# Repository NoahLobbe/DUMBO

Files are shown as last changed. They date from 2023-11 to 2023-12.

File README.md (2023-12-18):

# DUMBO
**D**efinitely **U**seless **M**ouse ro**B**ot **O**kay.

Project built off an RC car. Unsure of this specifics as I bought it a second hand shop (bargain!) eons ago (in a galaxy far, far away...).
These are my two guesses, but I think the FCC had other RC cars with similiar chassis, so really hard to find the exact one.
- Scientific Toys (n.d.), *R/C 2.4GHz 1:12 Sand Blaster*, http://www.scientific.com.hk/en/products/97213, accessed 24 May 2023
- FCC (2017), *FCC ID BY35058-24GR R/C Vehicle by Scientific Toys Ltd.*, FCC ID, https://fccid.io/BY35058-24GR, accessed 24 May 2023

## Design Process
Contains concept sketches, mechanical drawings (hand drawn), schematics, and flowchart. Some basic pieces of the design process.

## Protoype
All inside the folder `Prototype`. 
- Contains an .STL to 3D print to hold the rear assembly, of the RC car, in place, replacing the need of the original chassis cover.
- Code is a bit of a mess, so attempt to understand at your own peril.

## Finals
BEWARNED, things are messy; view at your own peril :D

### 3D Printing
Contains .STL's and some slicing images

### Code
`powerHD-1501MG` is the testing code to calibrate/check the servo is steering correctly.
`Version3_reversing attempt` and `Version4` were coded to use two shift registers in, cascaded. However, they were not needed in the final DUMBO. `shift_registers` is a testing file to make sure they are working, and make it easier to debug, compared to integrating it straight into the main code and figuring out "what the HECK is wrong?!??!?".
`Version6` is the last version. During testing, two Ultrasonics were needed to be registered stuck for DUMBO to be stuck, but performance might be better with only one required. Dunno.

### Images
Here are some:
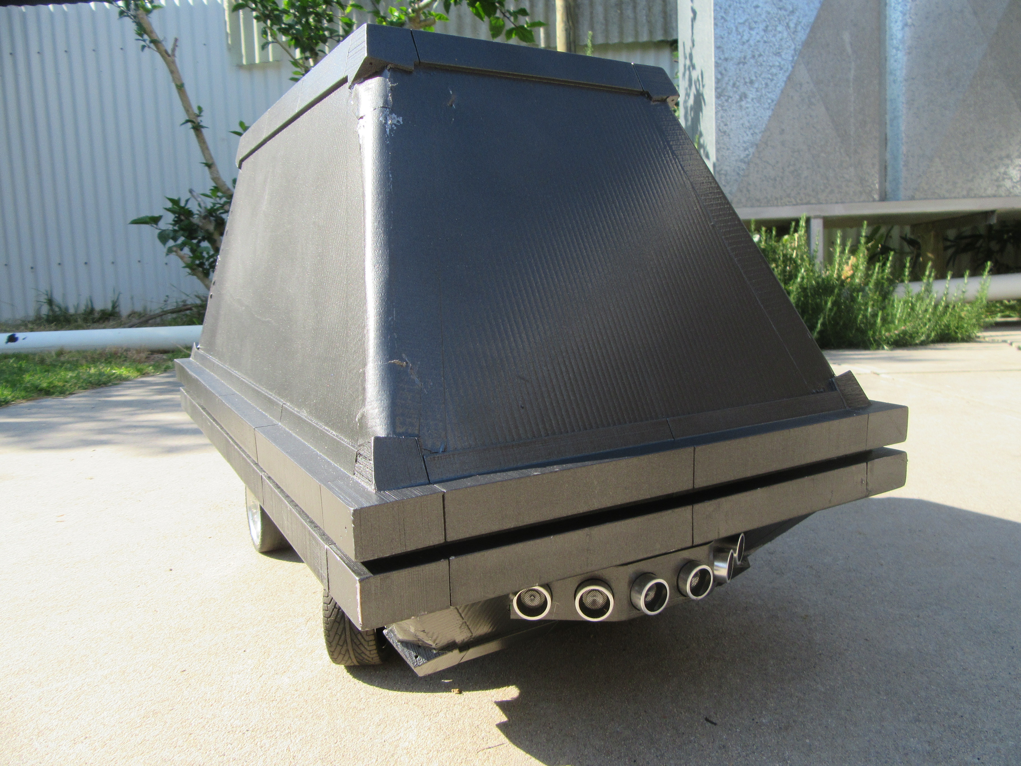
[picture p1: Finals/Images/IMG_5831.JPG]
DUMBO angled image

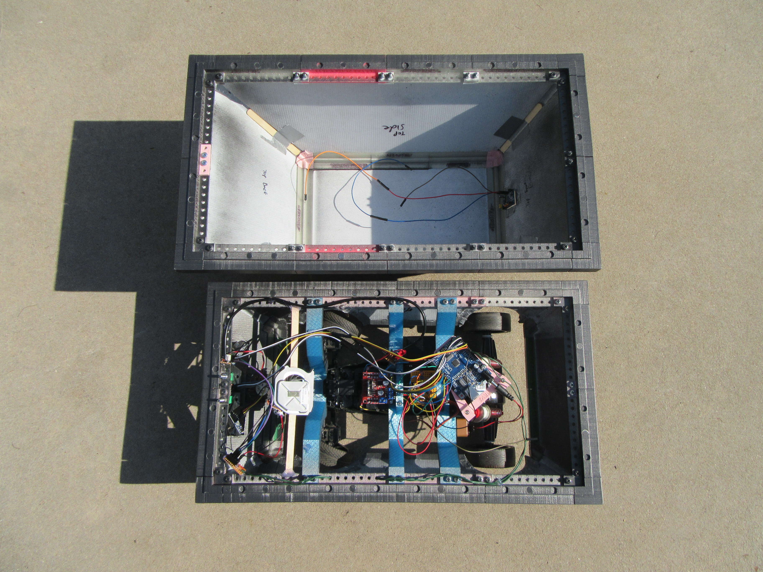
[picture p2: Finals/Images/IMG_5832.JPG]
DUMBO insides

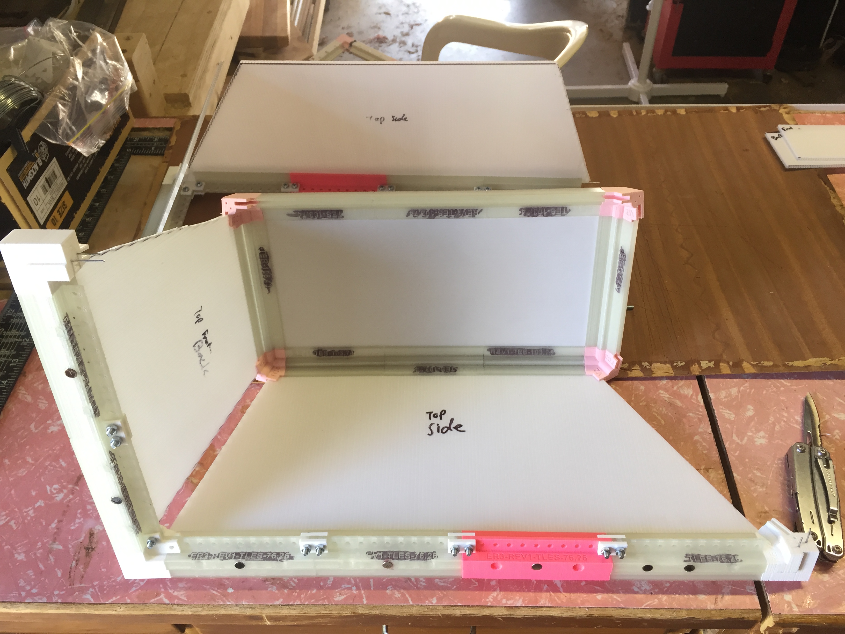
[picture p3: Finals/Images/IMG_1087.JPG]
Top Shell under construction


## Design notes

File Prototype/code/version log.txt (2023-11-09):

Last updated 24 August 2023, Noah Lobbe

How version system works, V.W.XY.Z
 * V is either 'b' or 'm' to indicate a branch or master
 * W is iteration of completed product.
 * X is incremented when a big function/feature/sensor is added
 * Y is just code improvements, no new stuff as that would classify as X
 * Z is the name of the branch, or if master than just = 0

Version log
master
	| m.0.10.0 Added motor driver
	|
	| m.0.11.0 Moved motor driver code into a neat class
	|
	| m.0.20.0 Added PIR motion sensor
	|
	| m.0.21.0 Moved PIR motion sensor code into a neat class
	|	
	| m.0.30.0 Added Ultrasonic sensor
	|
	| m.0.31.0 Code modifications
	| 
	| m.0.32.0 More code modifications. Note for previous versions: if (distance <=minimum_turning_distance_mm) is in wrong spot to ever be executed...

branch_rebuild ##############make sure to mention this annoying bug in final solution
	| b.0.30.rebuild Stripping back to basics. PIR not implemented in main loop.
	|
	| b.0.40.rebuild Reintroducing previous_distance stuff

//really need to add an encoder to the motor output to determine travel distances//

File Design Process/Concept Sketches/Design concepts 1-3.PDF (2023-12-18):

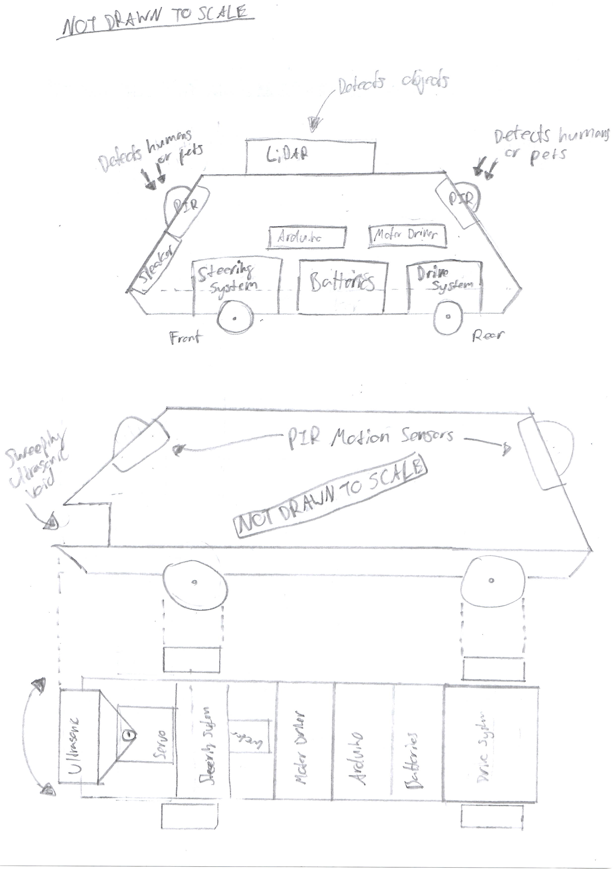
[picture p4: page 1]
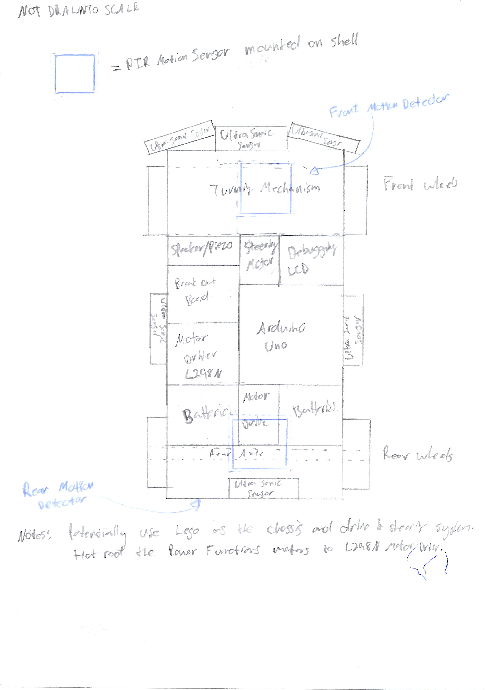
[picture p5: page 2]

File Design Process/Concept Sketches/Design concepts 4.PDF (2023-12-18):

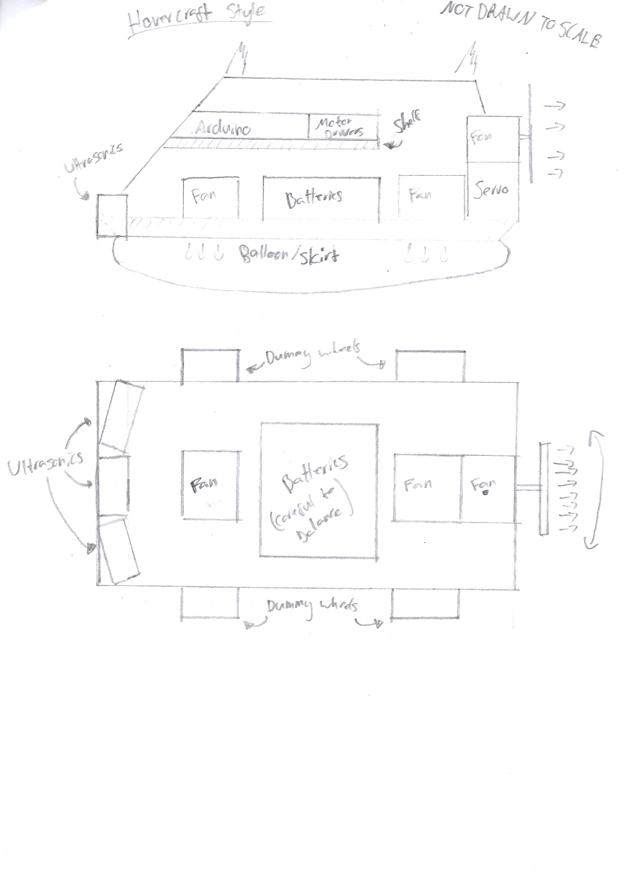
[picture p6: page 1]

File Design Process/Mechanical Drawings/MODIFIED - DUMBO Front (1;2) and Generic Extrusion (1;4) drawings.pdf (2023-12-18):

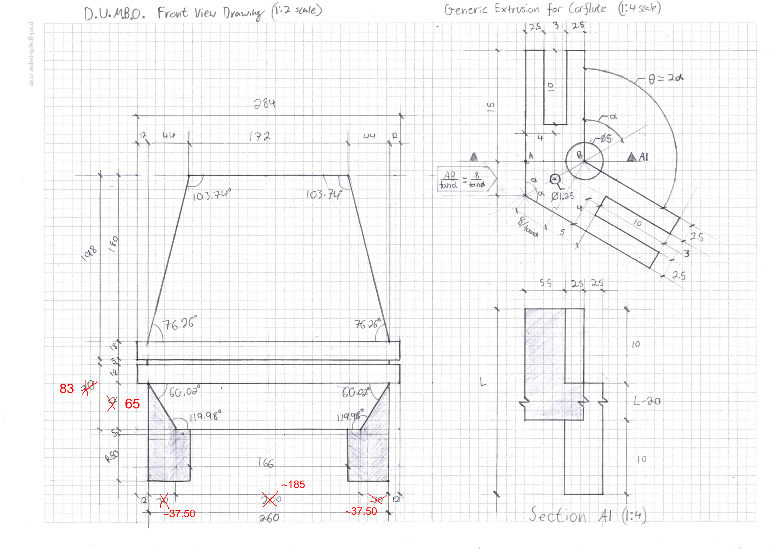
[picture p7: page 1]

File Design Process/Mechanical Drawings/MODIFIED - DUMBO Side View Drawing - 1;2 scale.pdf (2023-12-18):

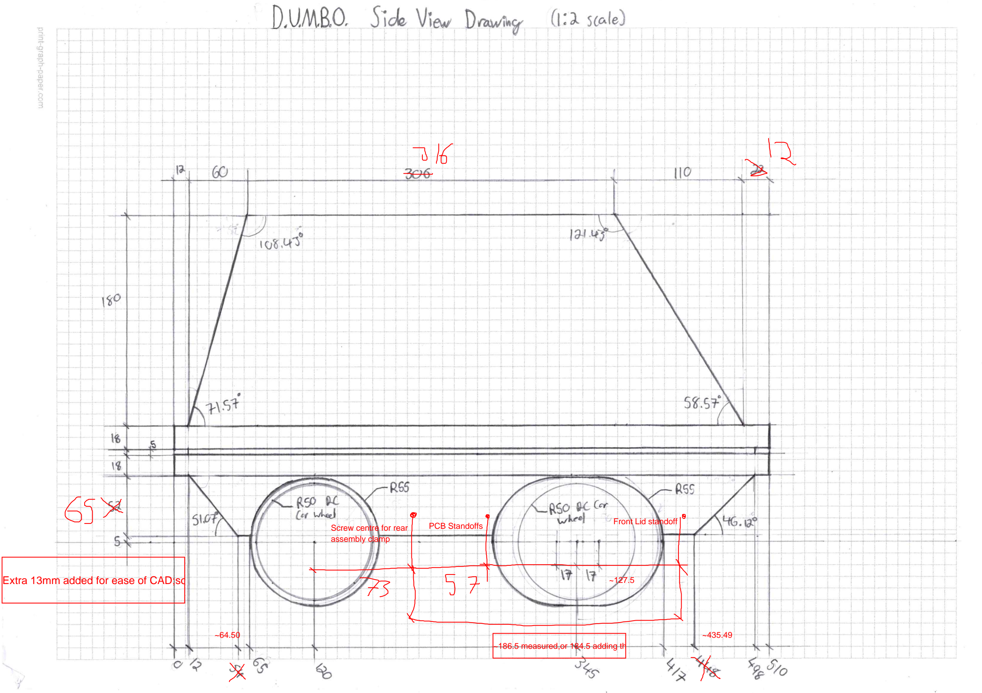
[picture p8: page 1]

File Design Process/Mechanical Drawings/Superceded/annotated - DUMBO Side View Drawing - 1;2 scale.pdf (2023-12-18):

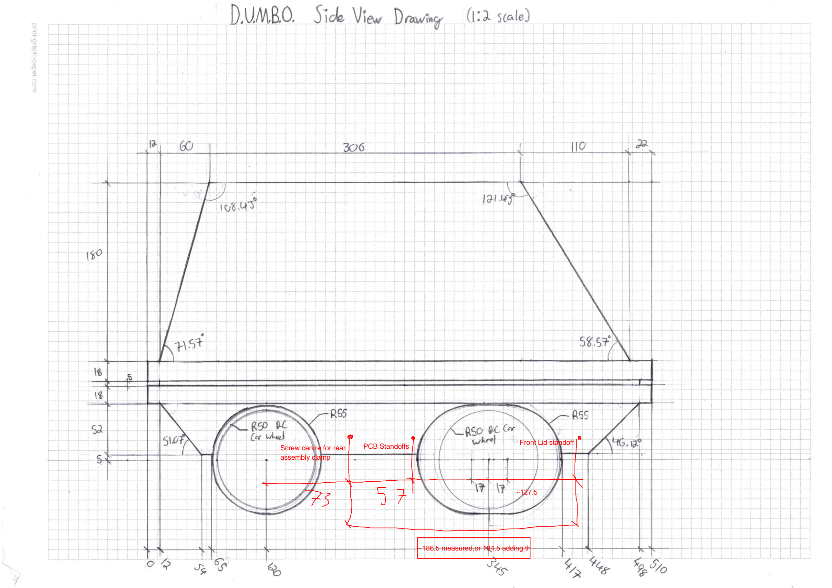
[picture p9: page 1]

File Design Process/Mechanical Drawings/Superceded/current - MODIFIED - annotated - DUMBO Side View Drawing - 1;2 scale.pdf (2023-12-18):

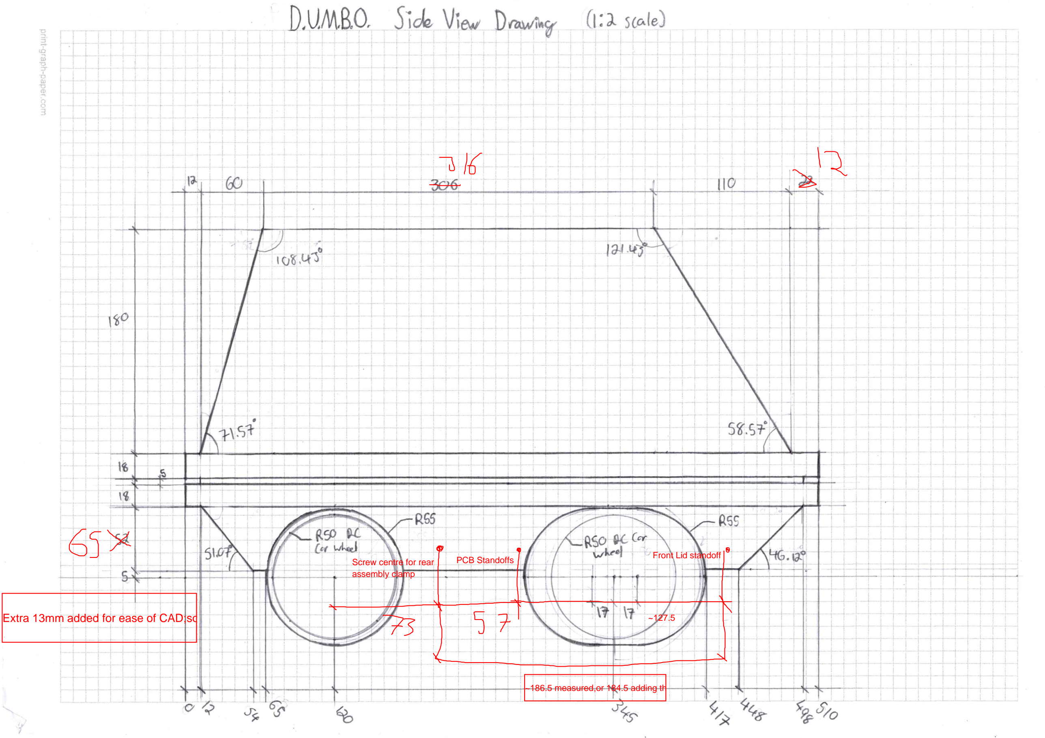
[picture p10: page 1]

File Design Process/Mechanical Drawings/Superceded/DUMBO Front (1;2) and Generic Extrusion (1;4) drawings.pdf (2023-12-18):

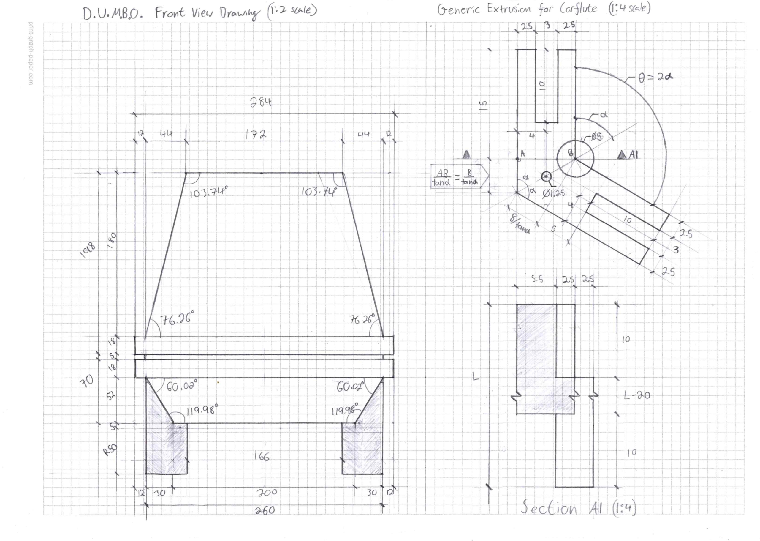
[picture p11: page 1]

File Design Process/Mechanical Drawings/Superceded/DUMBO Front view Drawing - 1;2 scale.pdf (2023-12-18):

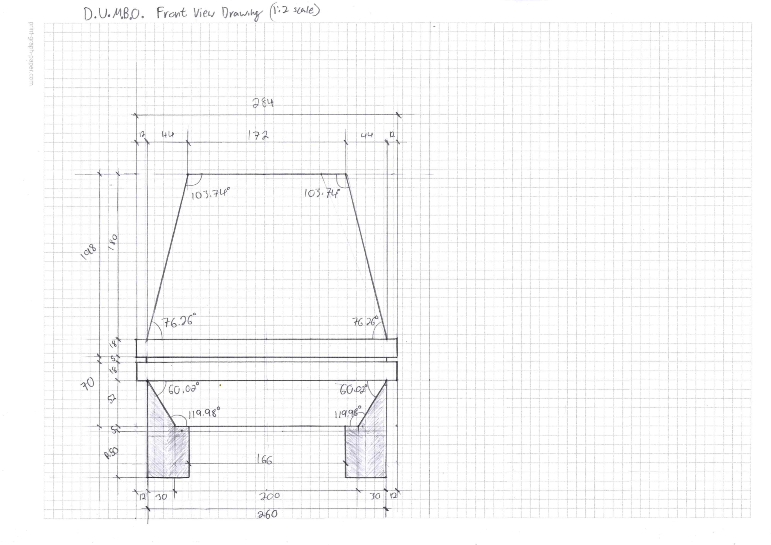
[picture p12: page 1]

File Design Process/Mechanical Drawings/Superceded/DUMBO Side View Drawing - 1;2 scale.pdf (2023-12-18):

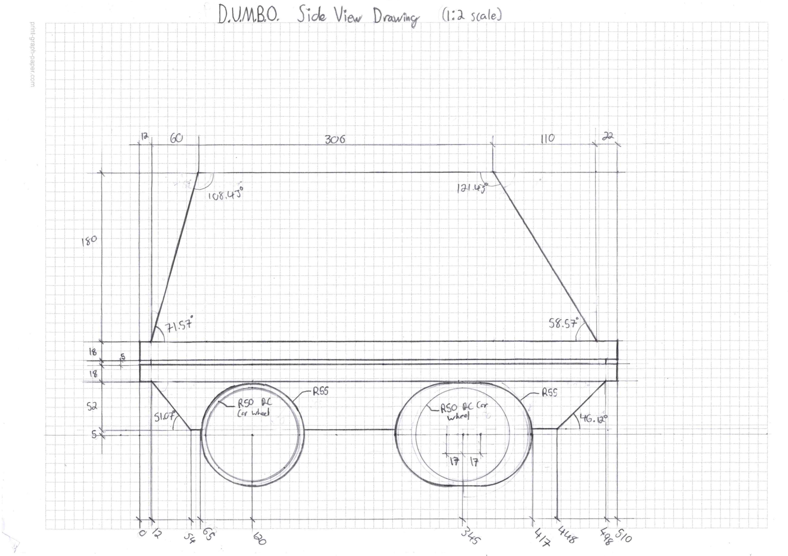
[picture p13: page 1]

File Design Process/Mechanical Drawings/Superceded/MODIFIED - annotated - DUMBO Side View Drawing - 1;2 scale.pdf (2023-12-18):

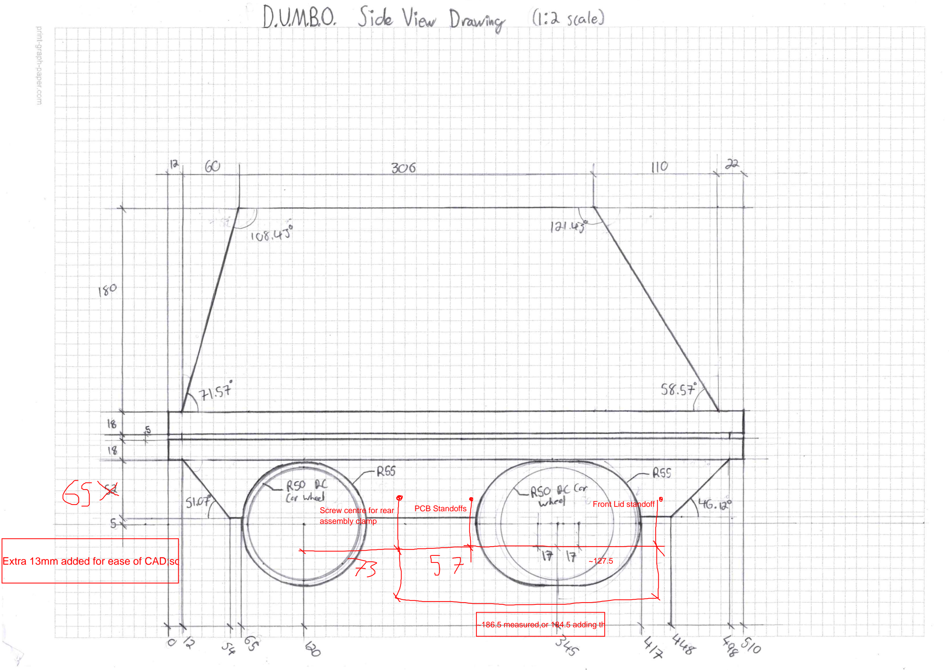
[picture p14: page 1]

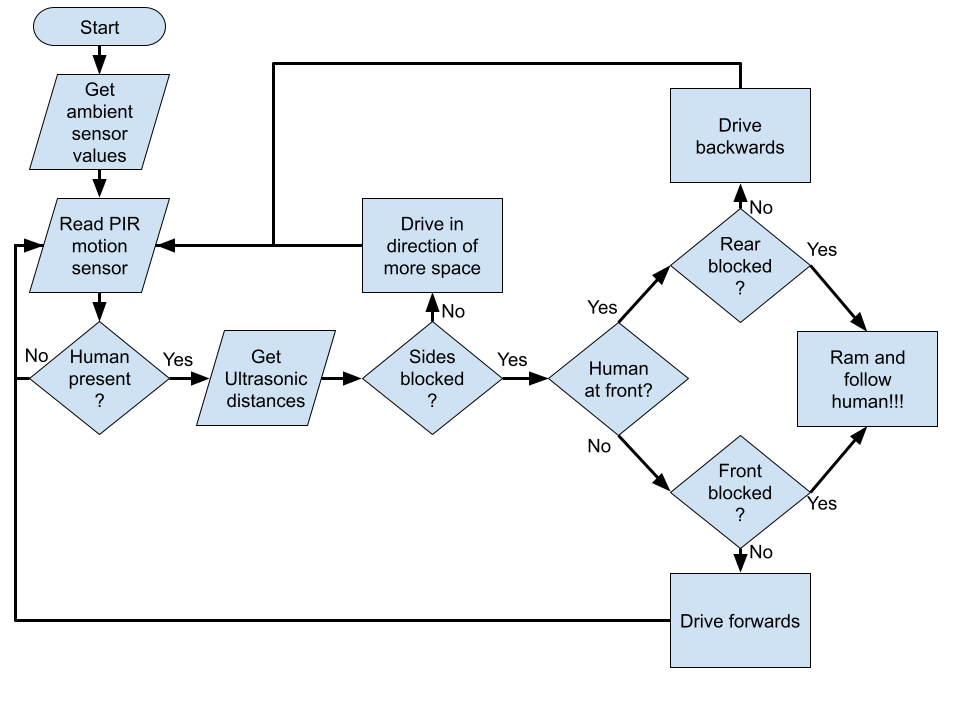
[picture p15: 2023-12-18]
Design Process/Flowchart/Program Flowchart - Major Product 2023.png

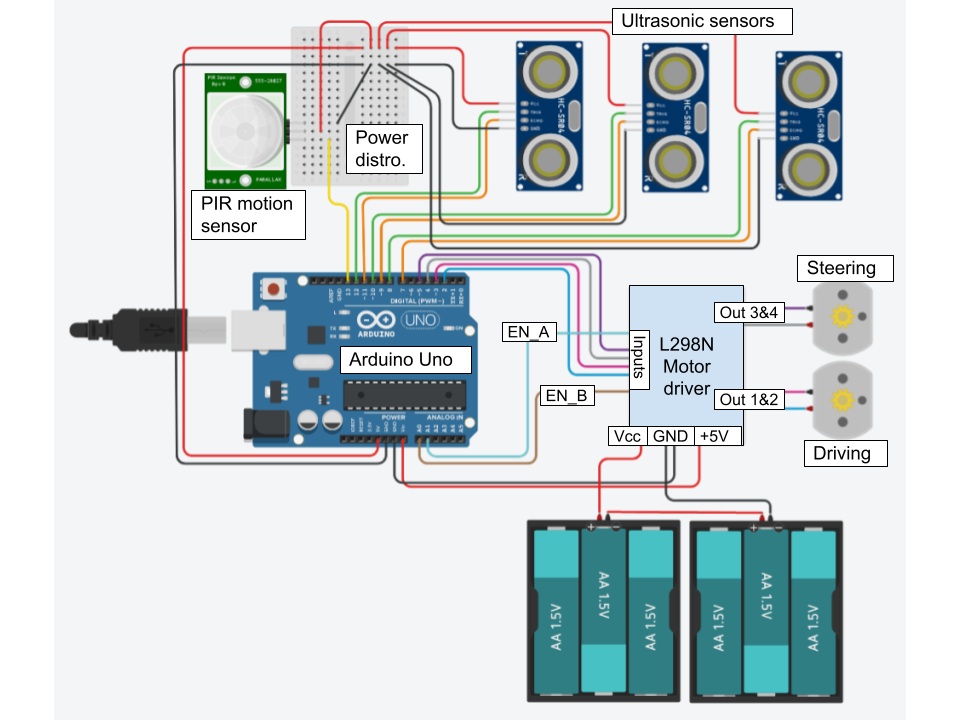
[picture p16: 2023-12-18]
Design Process/Schematic or fritzing/Fritzing for Useless Mouse Droid.png

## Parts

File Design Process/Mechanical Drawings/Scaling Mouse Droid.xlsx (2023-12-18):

Mouse Droid Dimensions |  |  |  |  | RC Car
 |  |  |  |  | width | 260
 |  |  |  |  | length | 325
Dimension | Value (mm) | Scale | Scaled Value (mm) |  | wheelbase | 225
Bottom Shell
Overall Length | 561.20 | 0.90 | 506.99
Pre-overhang length | 535.40 | 0.90 | 483.68
bottom length | 451.14 | 0.90 | 407.56
 |  | 0.90 | 0.00
Overall Width | 313.60 | 0.90 | 283.31
Pre-overhang width | 287.80 | 0.90 | 260.00
bottom Width | 219.80 | 0.90 | 198.57
 |  | 0.90 | 0.00
Overall height | 77.40 | 0.90 | 69.92
bottom-overhang height | 57.20 | 0.90 | 51.67
 |  | 0.90 | 0.00
Overhang depth | 12.90 | 0.90 | 11.65
Overhang height | 20.20 | 0.90 | 18.25
 |  | 0.90 | 0.00
Rear slope angle (from horizontal, measured from bottom) | 56.51 | 0.90 | 51.05
Front slope angle (from horizontal, measured from bottom) | 50.94 | 0.90 | 46.02 |  | Value | Scaled |  | Value | Scaled
 |  | 0.90 | 0.00 | Degrees | 0.9862855603 | 0 | Radians | 37.84549887 | 0 | Horizontal component
 |  | 0.90 | 0.00 | Degrees | 0.889070721 | 0 | Radians | 46.41890985 | 0 | Horizontal component
 |  | 0.90 | 0.00
 |  | 0.90 | 0.00
Arch centre-centre | 306.70 | 0.90 | 277.07
Rear arch radius | 57.20 | 0.90 | 51.67
Front arch radius | 32.60 | 0.90 | 29.45 |  |  |  |  |  | Value | Dimension
Distance from arch centres to bottom | 11.56 | 0.90 | 10.45 |  |  |  |  |  | 86.50 | L
 |  | 0.90 | 0.00 |  |  |  |  |  | 57.20 | r_1
Wheel arch spacing | 220.20 | 0.90 | 198.93 |  |  |  |  |  | 32.60 | r_2
Edge of bottom to rear arch | 12.90 | 0.90 | 11.65 |  |  |  |  |  | 0.2035 | a (angle in radians)
Edge of bottom to front arch | 45.04 | 0.90 | 40.69 |  |  |  |  |  | 0.3626 | c (angle in radians)
 |  | 0.90 | 0.00 |  |  |  |  |  | 11.56 | r_1 sina
Length of rear arch chord | 112.04 | 0.90 | 101.22 |  |  |  |  |  | 11.56 | r_2sinc
Length of front arch chord | 60.96 | 0.90 | 55.07 |  |  |  |  |  | 56.02 | r_1cosa
 |  | 0.90 | 0.00 |  |  |  |  |  | 30.48 | r_2cosc
height from rear arch top to overhang | 11.56 | 0.90 | 10.45
height from front arch top to overhang | 36.16 | 0.90 | 32.67
 |  | 0.90 | 0.00
Top Shell |  | 0.90 | 0.00
Overall Length | 559.5 | 0.90 | 505.46
top length | 324.2 | 0.90 | 292.88
back slope horizontal length | 66.8 | 0.90 | 60.35
front slope horizontal length | 118.3 | 0.90 | 106.87
 |  | 0.90 | 0.00
Overall width | 311.6 | 0.90 | 281.50 |  |  |  |  |  | Value | Dimension
top width | 161.8 | 0.90 | 146.17 |  |  |  |  |  | 1.308996939 | angle of sides from horizontal folded down (in radians)
one side slope width | 48.50 | 0.90 | 43.81
 |  | 0.90 | 0.00
post lip width | 258.80 | 0.90 | 233.80
 |  | 0.90 | 0.00
overall height | 200.7 | 0.90 | 181.31
height exlcluding lip | 181 | 0.90 | 163.52
 |  | 0.90 | 0.00
lip height | 19.7 | 0.90 | 17.80
lip depth (sides) | 26.40 | 0.90 | 23.85
lip depth (back) | 24.9 | 0.90 | 22.49
lip depth (front) | 25.3 | 0.90 | 22.86

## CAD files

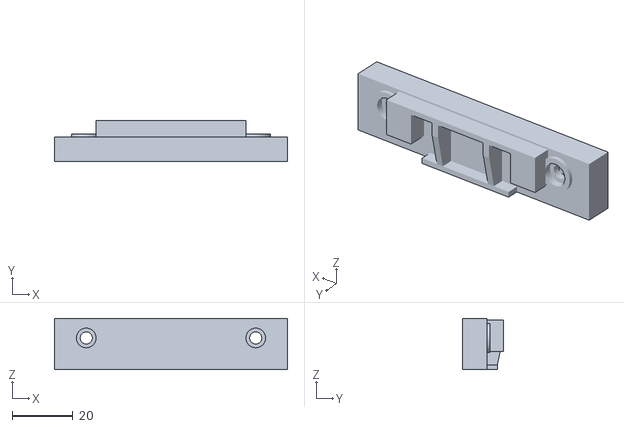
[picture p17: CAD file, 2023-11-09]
Prototype/RC car Rear Assembly Clamp.stl
77.0 x 13.5 x 17.0

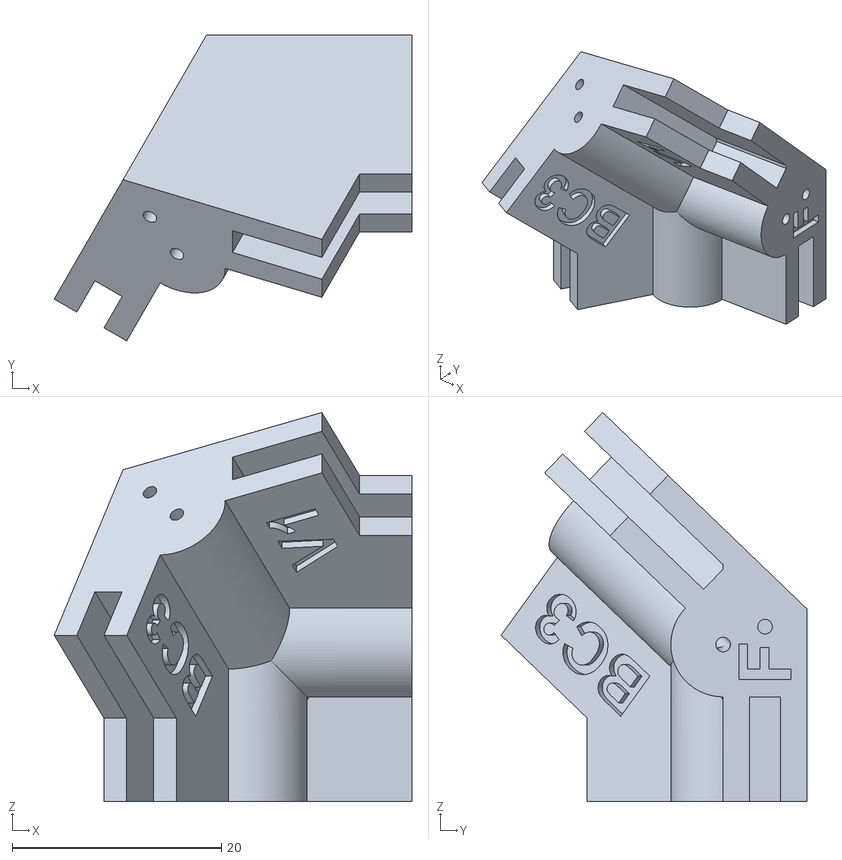
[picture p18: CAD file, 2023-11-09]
Finals/3D Printing/STLs/ER1 - Revision 1/ER1-Rev1-BCE3.stl
34.2 x 29.2 x 37.2

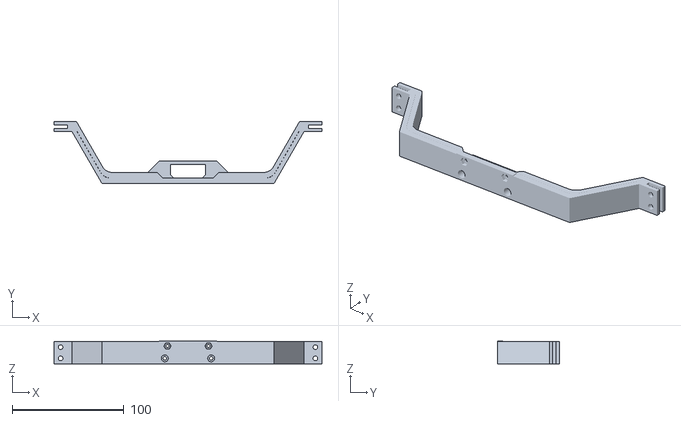
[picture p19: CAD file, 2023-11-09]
Finals/3D Printing/STLs/ER2 - Revision 2/ER2-Rev2-PCBSEB.stl
239.8 x 55.6 x 20.5

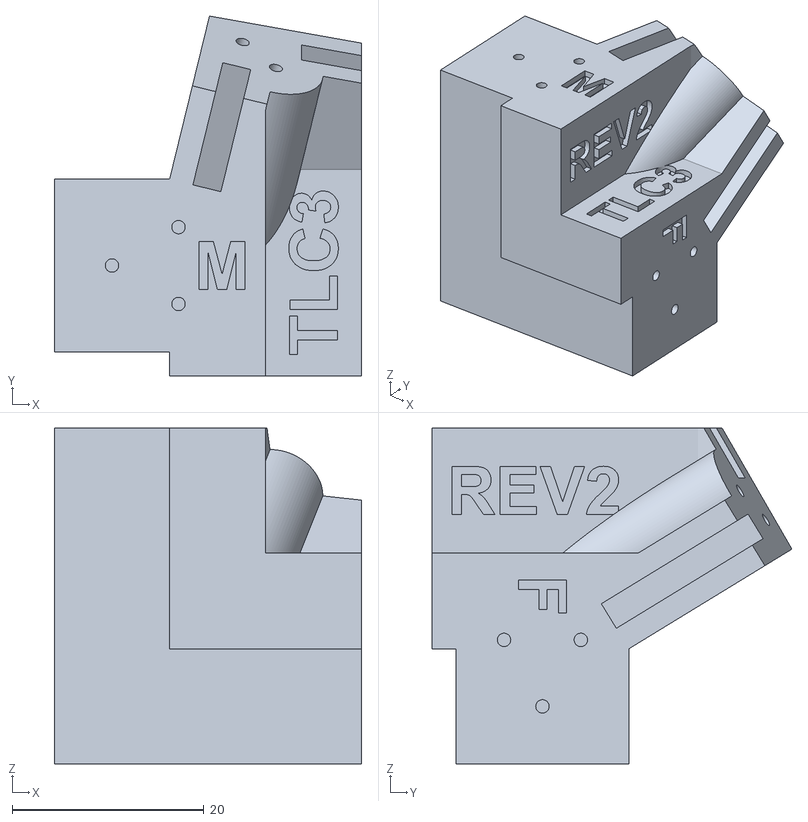
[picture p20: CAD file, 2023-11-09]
Finals/3D Printing/STLs/ER3 - Revision 2/ER3-Rev2-TLCE3.stl
32.0 x 37.5 x 35.0

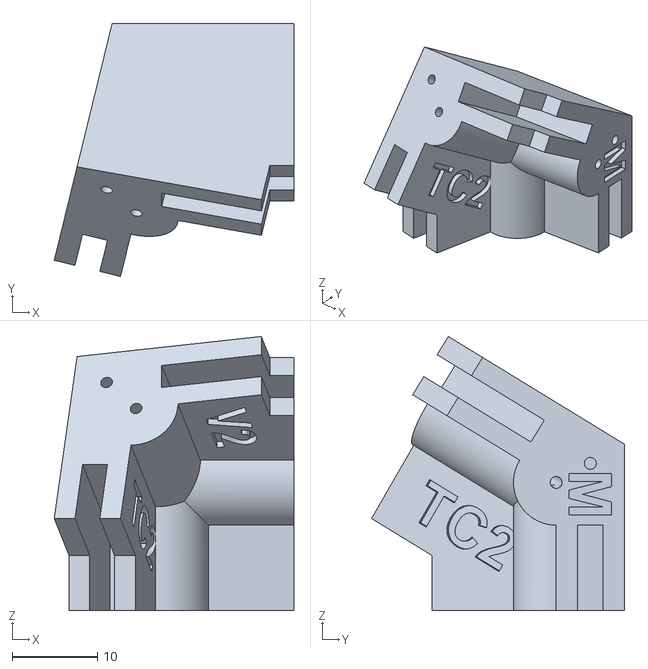
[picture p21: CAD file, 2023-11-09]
Finals/3D Printing/STLs/ER4 - Revision 2/ER4-Rev2-TCE2.stl
28.1 x 29.6 x 32.1

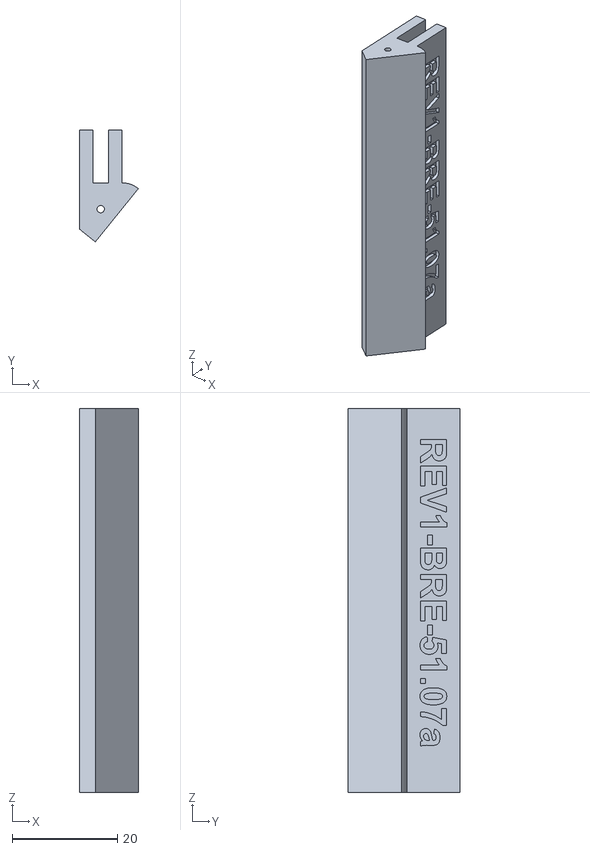
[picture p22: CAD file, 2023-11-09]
Finals/3D Printing/STLs/ER1 - Revision 1/ER1-Rev1-BRE-51.07a.stl
11.1 x 21.2 x 72.9

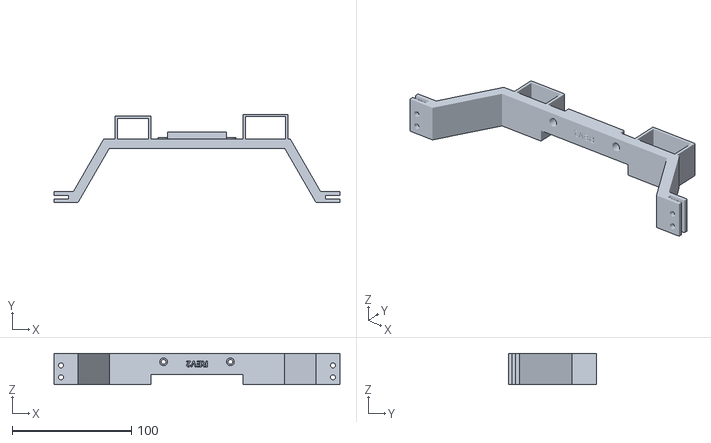
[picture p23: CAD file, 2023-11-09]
Finals/3D Printing/STLs/ER2 - Revision 2/ER2-Rev2-CRACEB.stl
239.8 x 74.1 x 26.0

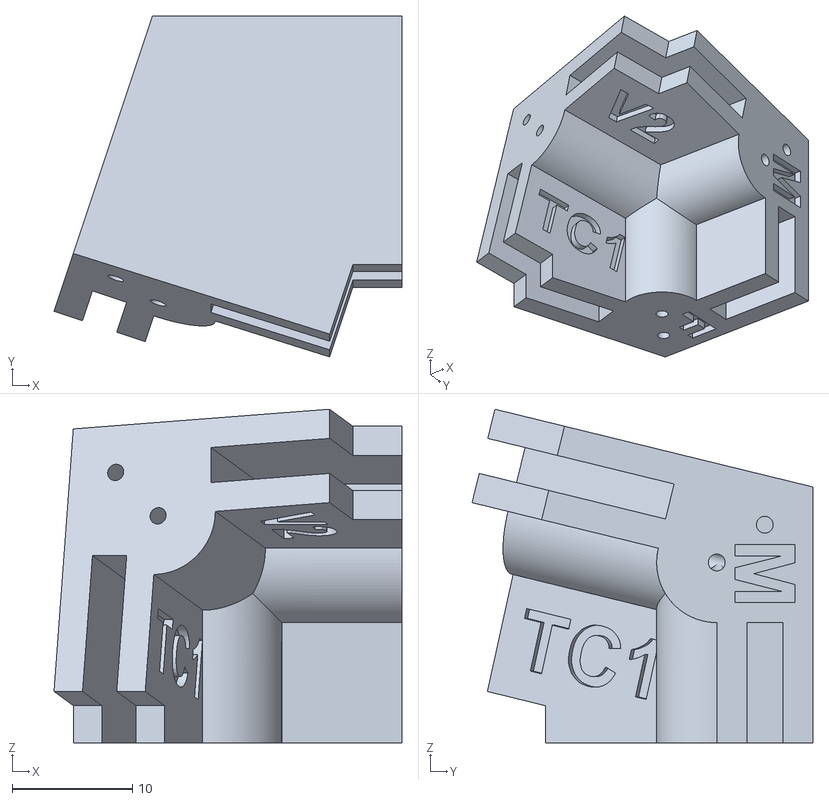
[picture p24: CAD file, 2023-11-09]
Finals/3D Printing/STLs/ER4 - Revision 2/ER4-Rev2-TCE1.stl
29.0 x 28.4 x 27.7

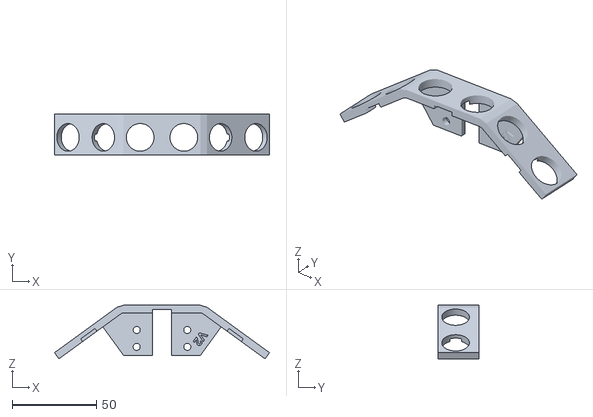
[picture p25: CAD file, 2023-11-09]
Finals/3D Printing/STLs/ER2 - Revision 2/ER2-Rev2-GUAEB.stl
127.5 x 24.6 x 31.8

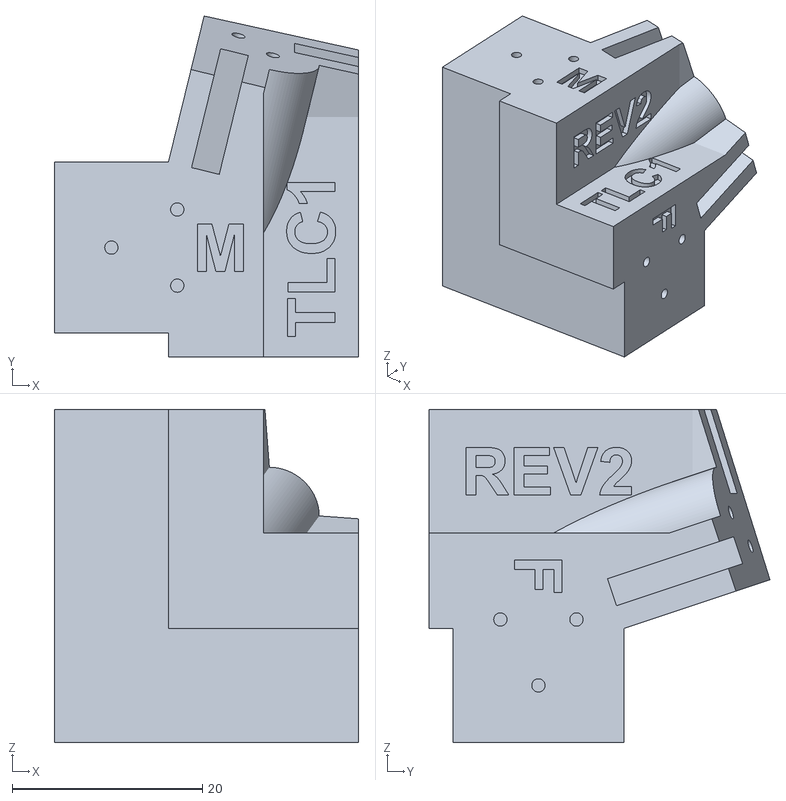
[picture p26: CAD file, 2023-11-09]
Finals/3D Printing/STLs/ER3 - Revision 2/ER3-Rev2-TLCE1.stl
32.0 x 35.8 x 35.0

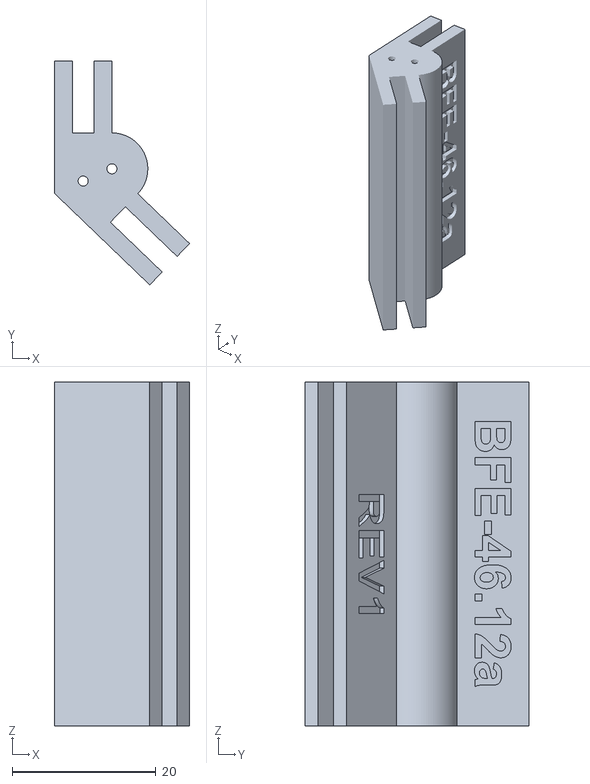
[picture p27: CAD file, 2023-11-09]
Finals/3D Printing/STLs/ER1 - Revision 1/ER1-Rev1-BFE-46.12a.stl
18.8 x 31.2 x 47.9

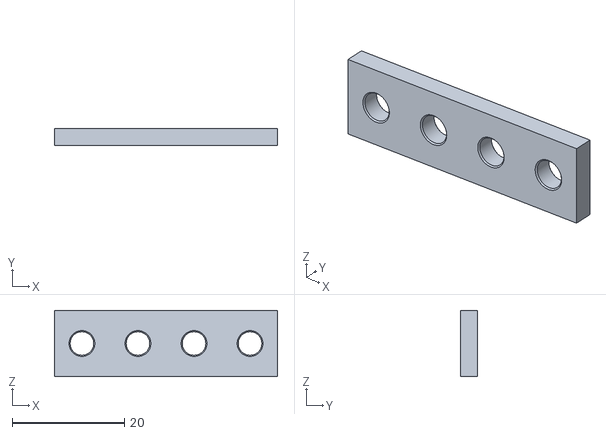
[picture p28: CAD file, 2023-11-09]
Finals/3D Printing/STLs/ER2 - Revision 2/ER2-Rev2-EBC4.stl
39.8 x 3.00 x 11.8

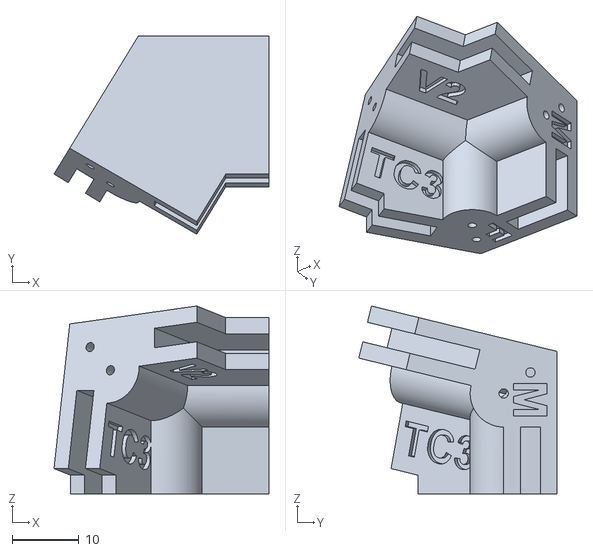
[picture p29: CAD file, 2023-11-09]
Finals/3D Printing/STLs/ER4 - Revision 2/ER4-Rev2-TCE3.stl
32.1 x 29.6 x 28.1

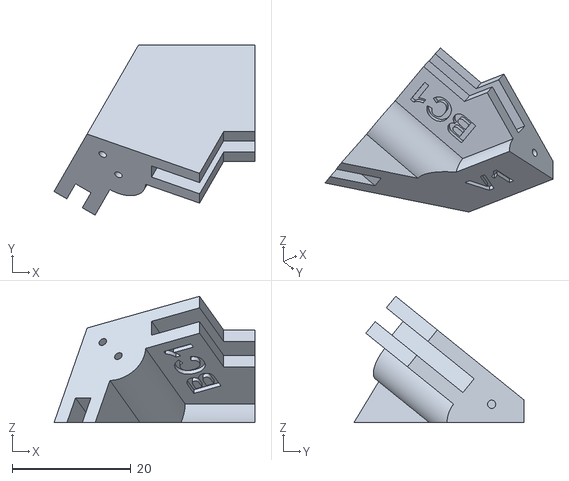
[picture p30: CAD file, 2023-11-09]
Finals/3D Printing/STLs/ER1 - Revision 1/ER1-Rev1-BCE1.stl
33.9 x 28.7 x 21.3

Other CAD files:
Finals/3D Printing/STLs/ER3 - Revision 2/ER3-Rev2-TLCE2.stl
Finals/3D Printing/STLs/ER1 - Revision 1/ER1-Rev1-BCE2.stl
Finals/3D Printing/STLs/ER4 - Revision 2/ER4-Rev2-TCE4.stl
Finals/3D Printing/STLs/ER3 - Revision 2/ER3-Rev2-TLCE4.stl
Finals/3D Printing/STLs/ER1 - Revision 1/ER1-Rev1-BCE4.stl
Finals/3D Printing/STLs/ER2 - Revision 2/ER2-Rev2-ArdBrckt.stl
Finals/3D Printing/STLs/ER2 - Revision 2/ER2-Rev2-CFB.stl
Finals/3D Printing/STLs/ER2 - Revision 2/ER2-Rev2-PIL10.stl
Finals/3D Printing/STLs/ER2 - Revision 2/ER2-Rev2-PIL15.stl
Finals/3D Printing/STLs/ER2 - Revision 2/ER2-Rev2-SLEB.stl
Finals/3D Printing/STLs/ER3 - Revision 1/ER3-Rev1-EBC.stl
Finals/3D Printing/STLs/ER3 - Revision 1/ER3-Rev1-ELC.stl
Finals/3D Printing/STLs/ER3 - Revision 1/ER3-Rev1-TLEF-58.57.stl
Finals/3D Printing/STLs/ER3 - Revision 1/ER3-Rev1-TLER-71.57.stl
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

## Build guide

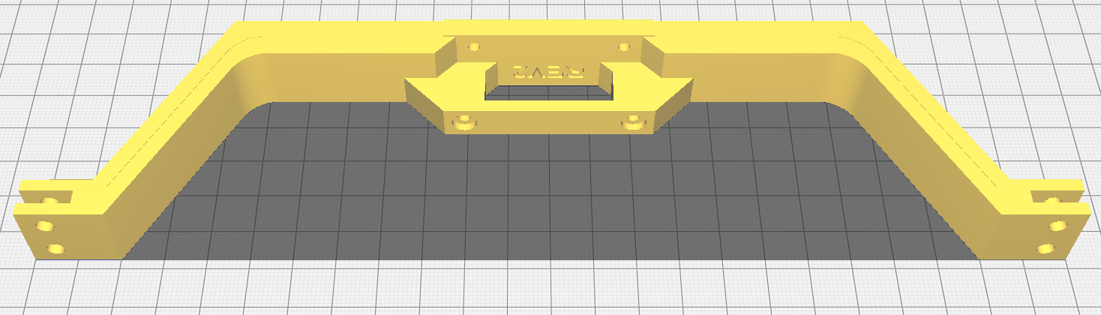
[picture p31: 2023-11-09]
Finals/3D Printing/STLs/ER2 - Revision 2/ER2-Rev2-PCBSEB print orientation.png

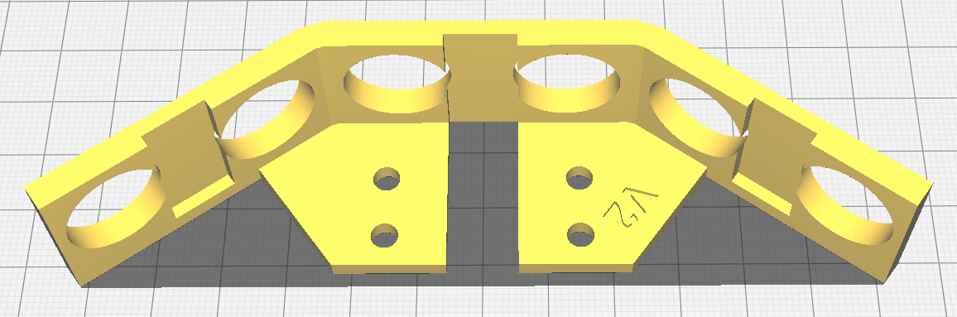
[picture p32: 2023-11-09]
Finals/3D Printing/STLs/ER2 - Revision 2/ER2-Rev2-GUAEB print orientation.png

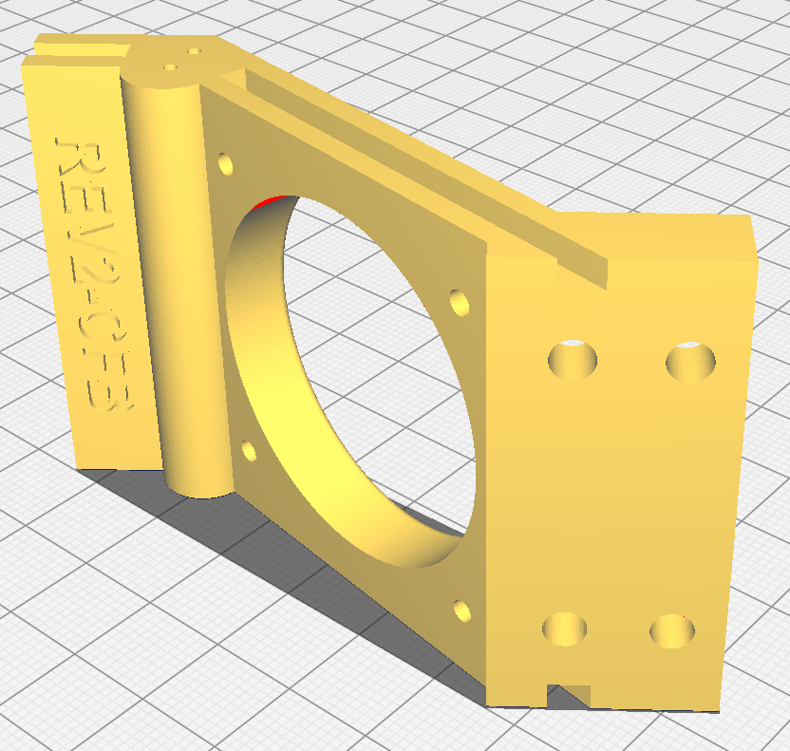
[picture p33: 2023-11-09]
Finals/3D Printing/STLs/ER2 - Revision 2/ER2-Rev2-CFB print orientation.png

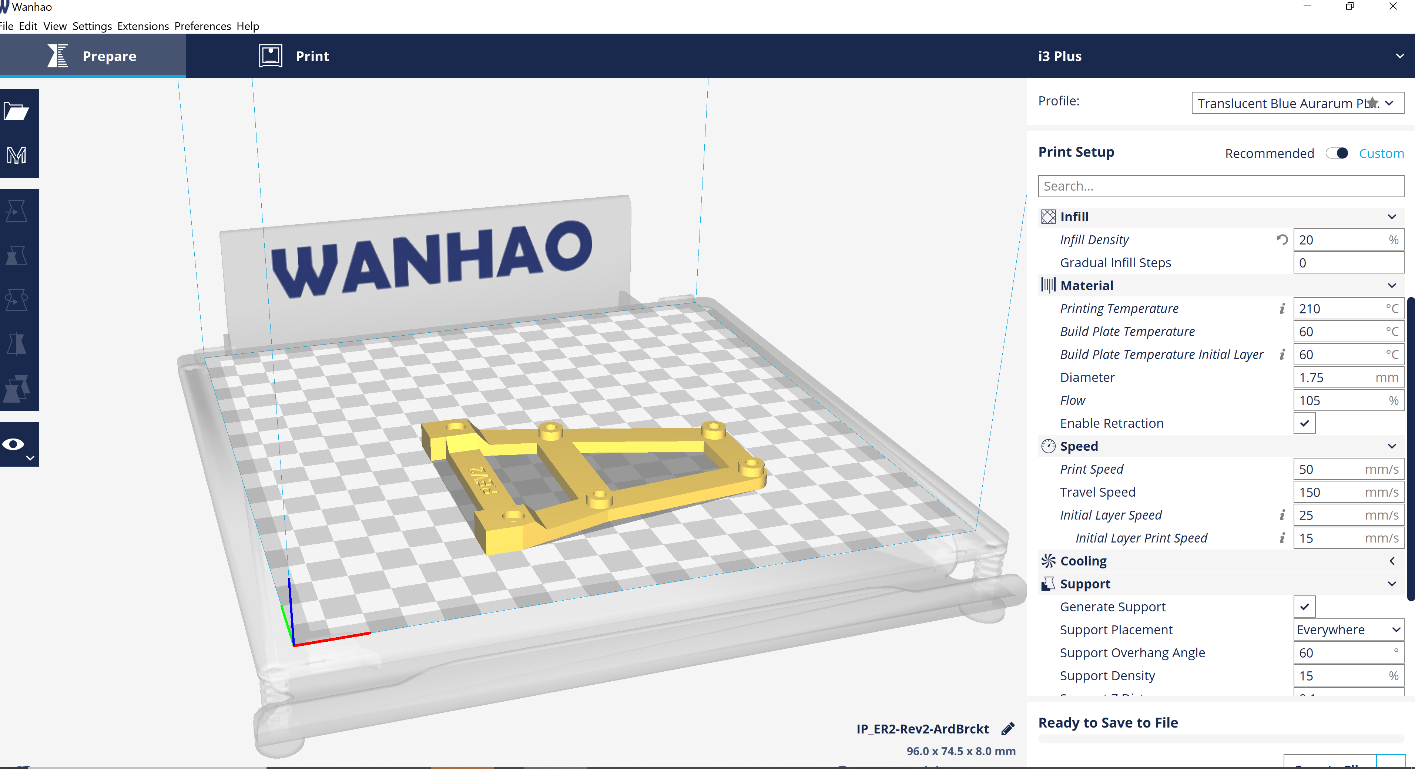
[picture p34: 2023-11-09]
Finals/3D Printing/Slicing Images/Slicing ER2-Rev2/ArdBrckt.png

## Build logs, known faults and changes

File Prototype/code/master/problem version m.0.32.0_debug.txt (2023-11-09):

29 august

Genuine Arduino used.
Code version is 0.32:	Sketch uses 6804 bytes (21%) of program storage space. Maximum is 32256 bytes. Global variables use 624 bytes (30%) of dynamic memory, leaving 1424 bytes for local variables. Maximum is 2048 bytes.

LED states explained:
- green LED (OBJECT_DETECTED_LED_PIN) turns on when an object less than 1100mm (object_avoidance_distance_threshold_mm) is detected.
- red LED (MOTION_LED_PIN ) not used currently
- blue LED (STUCK_LED_PIN) does exactly what it says on the tin.

Definitions:
- robot battery: batteries inbuilt for RC

After colliding with something/seeing that it is stuck, the blue LED stays on. Even after moving the robot such that it should be able to see it can move. Additional observation is that the 5V output on the Arduino drops to 3V and stays there during this period.
Current setup is powering the L298N IC logic from Arduino 5V.

Another test using VIN on Arduino to be an output powering L298N IC.
NOt just this case, but very prominant in this case was that when it bumped into something it reset. However, turning off the motor powersupply revealed that the Arduino was reseting and restarting by its self with no apparent reason. VIN still outputed ~5V. 9V battery used to power Arduino is at ~7V so still okay.

Powering the robot back on it was fine. Then it ran into a rosemary bush and couldn't see that it was stuck. Reset itself a couple of times, so I turned off the motor power supply to see if it was that; it was not, the Arduino reseting itself a couple of times more. Turned it off.

Transition back to using the L298N on board 5V regulator to see if it makes a difference. Thus, the vehicle battery powers everything (powering arduino through VIN from the L298N, now 5V output). It hit some pipe work and prevented it from moving and then it reset. It hit a chair and didn't reset till I picked it up then it appeared to be reseting itself. Tried again and it got stuck on grass and reset itself numerous times; a voltage reading showed that the L298N 5V output stayed at 5V.

A different Arduino (SMD IC)seemed to be better however, it did reset when robot stuck on grass but L298N still supplying ~5V for operation.

Now trying the SMD Arduino but powering it with the 9V battery like before with the original Arduino. Using proper 5V output to power L298N logic. Ran on to grass and hit a plastic chair and did NOT reset; potential fix?

Running the above again.Was doing fine till it hit the wooden screen, blue LED turned on (as well as green as expected) and stopped; however, moving it to a better position did nothing. Voltage check showed Arduino supplying 3.24V to L298N IC logic, and 4.9V on the 9V battery pre-Arduino (Arduino still running though). Just sitting there, with blue and green LEDs on. No wires loose. Robot batteries showing a normal 7.9V. Pressing the reset button, the Arduino just goes back to the same state. Turning off both power supplies. Turning them back on, the robot starts forward then stops returning to blue and green LED on. Another on and off repeats the last sentence. Nothing has been hot during this entire document.

PLugging in the Arduino to laptop to attempt to reinstall code, then turning on robot batteries, it starts functioning normally. Unplugging and turning off, it the RX LED starts blinking and then stops staying on, while not moving. Another on/off it starts forward then stops with blue and green LEDs on.

setting PRINT_RESULTS to false and re uploading. Starts off fine, runs into landing stops with blue and green LEDs on; its 'locked up' again. Voltages at this point are:
- Residual 1.38V between L298N 12V and GND
- 7.14V for 9V battery
- 7.89V robot battery
- 3.3V (on 5V output) for Arduino when turned on (started then locked up again).

Re testing with just a simple motor driver control program using Serial, when robot stuck doesn't reset Arduino. Adding `RC_Car.drive('F', 255);` to test if the laptop power is changing things. No reseting problem. Still locked up though.

In summary, primary problem is the unapparent 'lock up' and then also the reseting problem. 

Commented out `else if (withinTolerance(distance_mm, prev_distance_mm, STUCK_TOLERANCE) && (distance_mm <= 400)) { //yes that is a hard coded number...
    return true;` from `isVehicleStuck(...)`
Did nothing. Still locked up with green and blue LED, but also locked up with just blue LED on.

Added blinking STUCK_LED_PIN (blue) LED to `else if (is_stuck) {...}`. Turned on, but not the robot supply, and it said it was stuck (blue blinking) but nothing was within STUCK_DISTANCE_MM.

Replaced Ultrasonic. Changed nothing.

Removed `timeout=0` in `pulseIn(...)`. It hit something and saw it was stuck, but never finished blinking. One reset later, it spontaneously thought it was stuck and stopped everything.

Uploading 0.31; still thought itself stuck, blue LED flickering. CIrcuit is slightly different to when 0.31 was made, that version had the arduino powered by L298N regulator

Changed power circuit so that Arduino was powered of L298N regulated 5V and it seemed to work better. Though a couple of small similar bugs still seem to be present, so code branch and rebuild is HIGHLY ADVISED

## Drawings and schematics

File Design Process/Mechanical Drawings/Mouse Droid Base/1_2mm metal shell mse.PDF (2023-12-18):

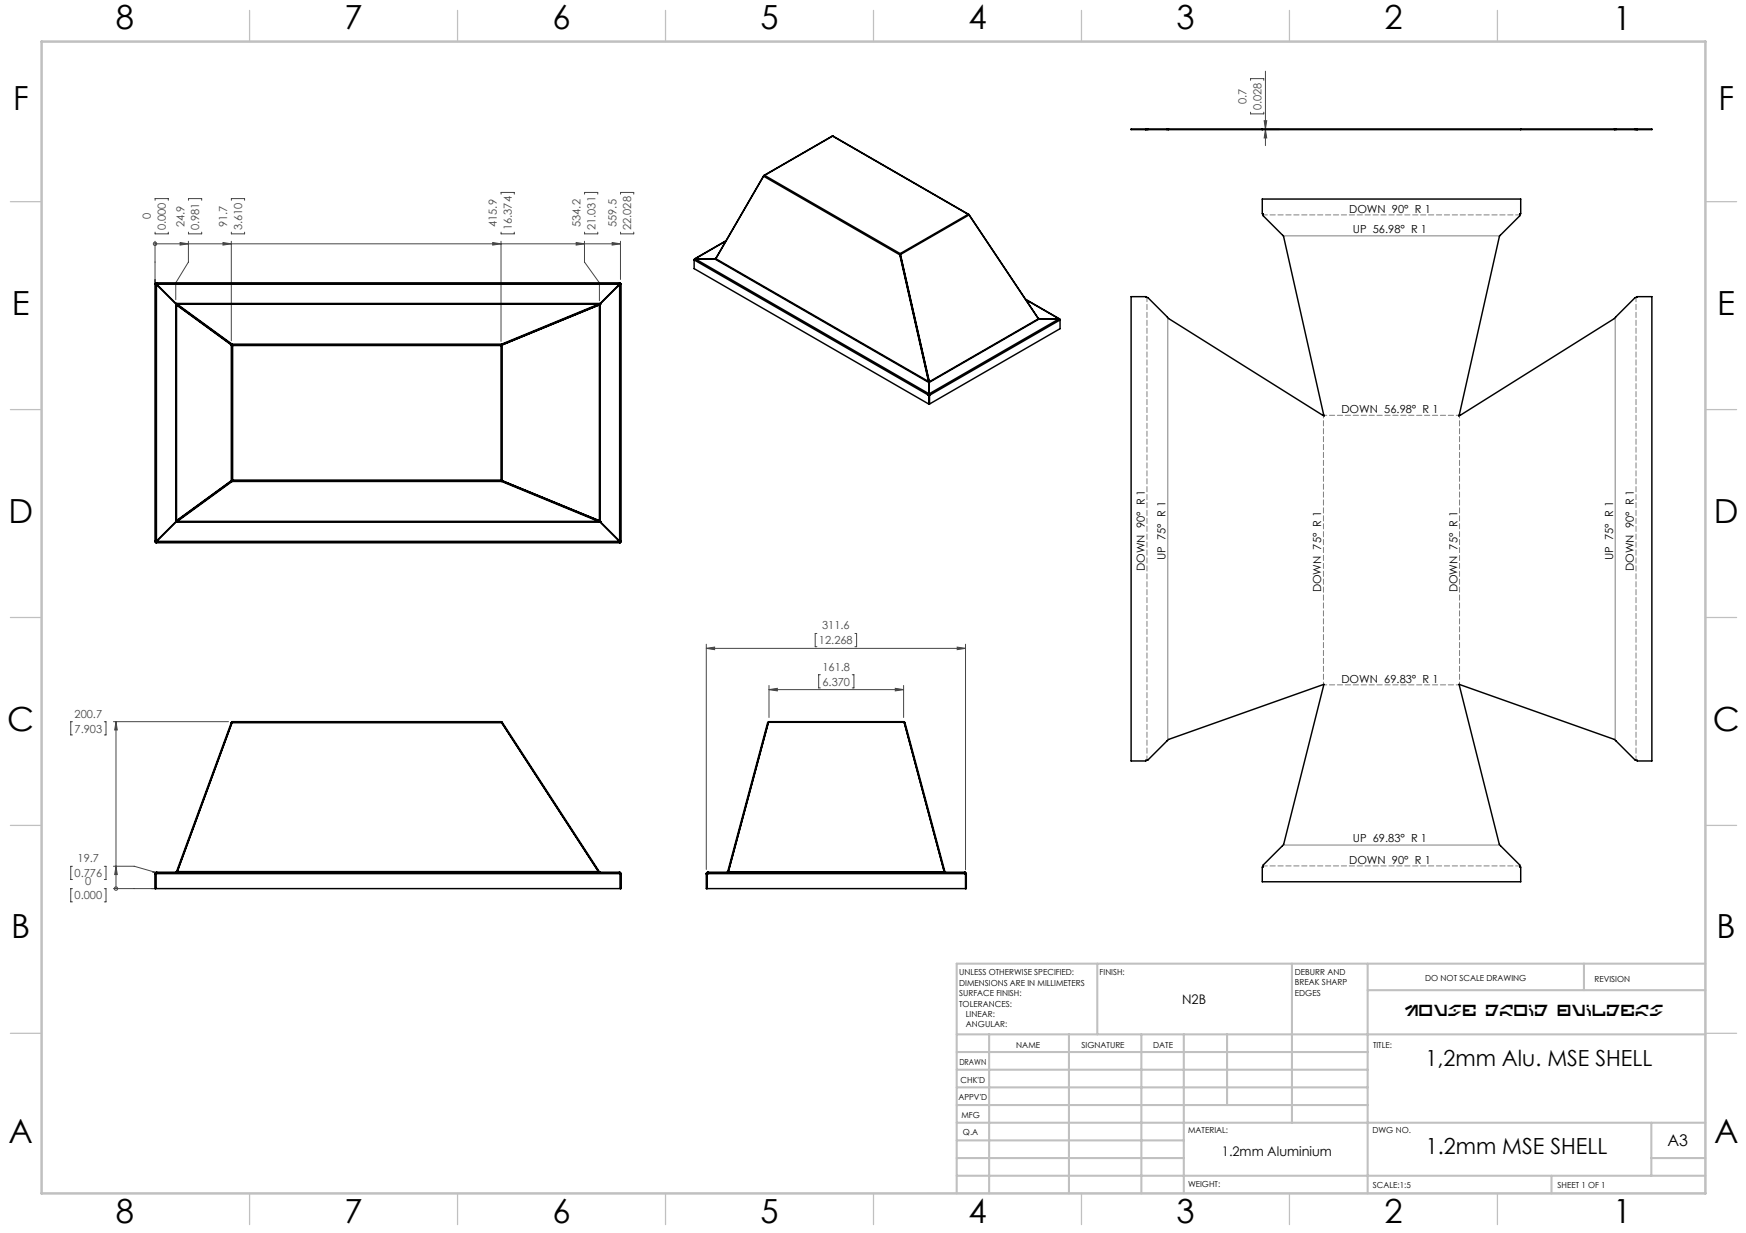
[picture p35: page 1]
DOWN 90° R 1; DOWN 90° R 1 UP 56.98° R 1; DOWN 69.83° R 1; DOWN 75° R 1; DOWN 56.98° R 1; FINISH:; DEBURR AND; BREAK SHARP; DO NOT SCALE DRAWING; REVISION; SCALE:1:5; SHEET 1 OF 1

UNLESS OTHERWISE SPECIFIED:
DIMENSIONS ARE IN MILLIMETERS
SURFACE FINISH:
TOLERANCES:
LINEAR:
ANGULAR:

MOUSE DROID BUILDERS

NAME | SIGNATURE | DATE | | | | TITLE: 1,2mm Alu. MSE SHELL

DRAWN
CHK'D
APPV'D
MFG
Q.A | | | | MATERIAL: | DWG NO. 1.2mm MSE SHELL | A3 1.2mm Aluminium

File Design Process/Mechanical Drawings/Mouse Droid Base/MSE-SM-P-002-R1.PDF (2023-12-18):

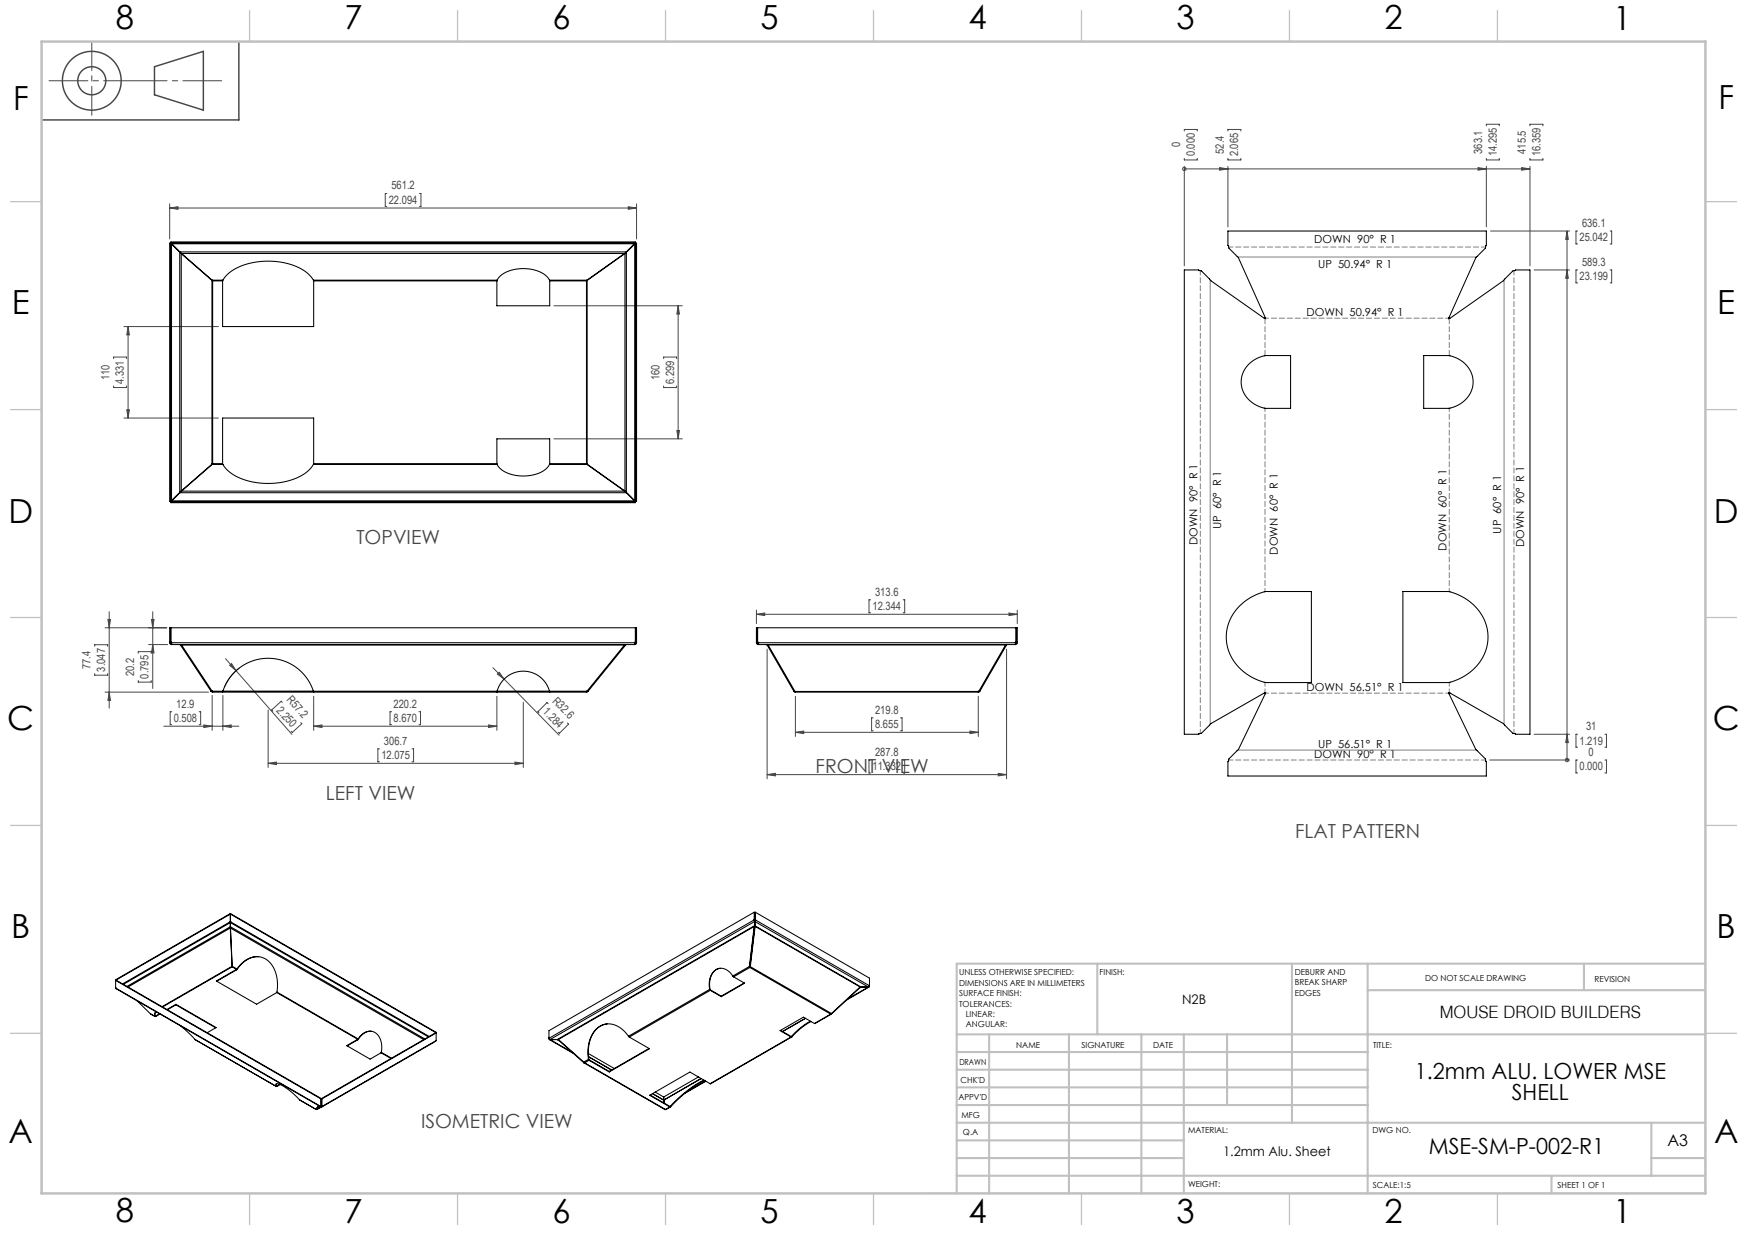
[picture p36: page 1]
LEFT VIEW; ISOMETRIC VIEW; DOWN 90° R 1; DOWN 56.51° R 1; DOWN 60° R 1; DOWN 50.94° R 1; FLAT PATTERN; FRONT VIEW; FINISH:; DEBURR AND; BREAK SHARP; DO NOT SCALE DRAWING; REVISION; SCALE:1:5; SHEET 1 OF 1

UNLESS OTHERWISE SPECIFIED:
DIMENSIONS ARE IN MILLIMETERS
SURFACE FINISH:
TOLERANCES:
LINEAR:
ANGULAR:

MOUSE DROID BUILDERS

NAME | SIGNATURE | DATE | | | | TITLE: 1.2mm ALU. LOWER MSE SHELL

DRAWN
CHK'D
APPV'D
MFG
Q.A | | | | MATERIAL: | DWG NO. MSE-SM-P-002-R1 | A3 1.2mm Alu. Sheet

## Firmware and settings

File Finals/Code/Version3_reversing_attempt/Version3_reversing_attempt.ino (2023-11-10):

/*
 * 
 */

////Libraries
#include "MotorSystem.h"
#include "Ultrasonic.h"
#include "Functions.h"
#include "CustomDataTypes.h"


////pin definitions
///motor system
#define EN_STEERING_SPEED_PIN 10
#define STEERING_MOTOR_A_PIN 4
#define STEERING_MOTOR_B_PIN 5

#define DRIVING_MOTOR_A_PIN 7
#define DRIVING_MOTOR_B_PIN 6
#define EN_DRIVING_SPEED_PIN 11


///Front ultrasonic array
#define NUM_F_U_SENSORS 3
const char F_ID_CHARS[NUM_F_U_SENSORS] = {'L','F','R'};

const uint8_t F_ECHO_PINS[NUM_F_U_SENSORS] = {A4,A2,A0};
const uint8_t F_TRIG_PINS[NUM_F_U_SENSORS] = {A5,A3,A1};

const uint8_t DIRECTION_LED_PINS[NUM_F_U_SENSORS] = {2,3,8};
const uint8_t ZERO_MEASUREMENT_LED_PIN = 9;
const uint8_t STUCK_LED_PIN = 12;



////variables and other constants
///general
#define PRINT_RESULTS false
#define MAX_NUM_STUCK 10
bool vehicle_is_definitely_stuck = false;
int8_t stuck_counter = 0;
bool stuck_flashing_state = false;


///motor system
#define VEHICLE_SLOW_SPEED_LED_PIN 13
#define PWM_SPEED_ENABLED true 
#define NORMAL_SPEED 200
#define SLOW_SPEED 128
uint8_t vehicle_speed = NORMAL_SPEED;

char curr_turn_direction = 'F'; 
char curr_drive_direction = 'F';
bool has_braked = false;



///Front ultrasonic array
#define PULSEIN_TIMEOUT_US 100000//the maximum time the pulseIn(...) function can take to wait for a signal. I think...
#define ACUTE_ANGLE_BETWEEN_SENSORS_RAD (36 * (PI/180)) //36degrees, converting
#define DIST_DIFFERENCE_MM round(22 * sin(ACUTE_ANGLE_BETWEEN_SENSORS_RAD)) //calculating the 'height' difference between the front and side sensors, from centre of side sensor (~22mm)

//loop update timing stuff
#define TIME_BETWEEN_U_SENSORS_MS 100 //ideally, 60ms between triggering an ultrasonic prevents wave interference 
unsigned long U_current_time_ms;
unsigned long U_previous_time_ms;

///Distance Stuff
#define LR_DIST_TOLERANCE_MM 100
#define STUCK_TOLERANCE_MM 10
#define STUCK_DISTANCE_MM 50 
const uint16_t F_STUCK_DISTANCES_MM[NUM_F_U_SENSORS] = {DIST_DIFFERENCE_MM+STUCK_DISTANCE_MM, STUCK_DISTANCE_MM, DIST_DIFFERENCE_MM+STUCK_DISTANCE_MM};
#define IGNORE_DISTANCE_THRESHOLD_MM 2000
#define SLOW_DOWN_DISTANCE_THRESHOLD_MM 1000
#define BRAKE_DISTANCE_THRESHOLD_MM 200
#define REVERSE_DISTANCE_MM 500

uint16_t curr_distances_mm[NUM_F_U_SENSORS];
uint16_t prev_distances_mm[NUM_F_U_SENSORS];
bool front_sensor_stuck_states[NUM_F_U_SENSORS];







////objects
MotorSystem RC_Car(PRINT_RESULTS);

Ultrasonic F_U_Sensors[NUM_F_U_SENSORS];




void setup() {
  ///motor system
  RC_Car.attach(STEERING_MOTOR_A_PIN, STEERING_MOTOR_B_PIN,  DRIVING_MOTOR_A_PIN, DRIVING_MOTOR_B_PIN);
  
  if (PWM_SPEED_ENABLED) {
    RC_Car.enablePWM(EN_STEERING_SPEED_PIN, EN_DRIVING_SPEED_PIN);
    pinMode(VEHICLE_SLOW_SPEED_LED_PIN, OUTPUT);
    
  } else {
    pinMode(EN_STEERING_SPEED_PIN, OUTPUT);
    pinMode(EN_DRIVING_SPEED_PIN, OUTPUT);
    digitalWrite(EN_STEERING_SPEED_PIN, HIGH); //default to max
    digitalWrite(EN_DRIVING_SPEED_PIN, HIGH); //default to max
  }
  
  ///Front ultrasonic array
  //LED indicators
  for (int i=0; i<NUM_F_U_SENSORS; i++) {
    pinMode(DIRECTION_LED_PINS[i], OUTPUT);
    digitalWrite(DIRECTION_LED_PINS[i], LOW);
  }
  pinMode(ZERO_MEASUREMENT_LED_PIN, OUTPUT);
  digitalWrite(ZERO_MEASUREMENT_LED_PIN, LOW);

  pinMode(STUCK_LED_PIN, OUTPUT);
  digitalWrite(STUCK_LED_PIN, LOW);

  //setup the sensors
  for (int i=0; i<NUM_F_U_SENSORS; i++) {
    F_U_Sensors[i].init(F_ECHO_PINS[i], F_TRIG_PINS[i], F_ID_CHARS[i]);
  }
  U_previous_time_ms = millis();


  ///Miscenialous stuff
  //so prev_distances_mm has something in it
  getDistances();
  copyArray(curr_distances_mm, prev_distances_mm, NUM_F_U_SENSORS);
  srand (millis());
  
  Serial.begin(115200);
  Serial.print("F_STUCK_DISTANCES_MM: ");
  Serial.println(strArray(F_STUCK_DISTANCES_MM, NUM_F_U_SENSORS, false));

  delay(1000);

}


void getDistances() {
  for (int i=0; i<NUM_F_U_SENSORS; i++) {
      curr_distances_mm[i] = F_U_Sensors[i].getDistanceMM(PULSEIN_TIMEOUT_US);
  }
}

bool isStuck() {
  for (uint8_t i=0; i<NUM_F_U_SENSORS; i++) {
    /*
    if ((curr_distances_mm[i] == 0) || (curr_distances_mm[i] > IGNORE_DISTANCE_THRESHOLD_MM)) {
      //false, can safely ignore stuff
    }
    */
    //sensor_stuck_states_array[i] = ( withinTolerance(curr_distances_mm[i], prev_distances_mm[i], STUCK_TOLERANCE_MM) && (curr_distances_mm[i] <= F_STUCK_DISTANCES_MM[i]) );
    bool within_tolerance = withinTolerance(curr_distances_mm[i], prev_distances_mm[i], STUCK_TOLERANCE_MM);
    bool within_stuck_dist = (curr_distances_mm[i] <= F_STUCK_DISTANCES_MM[i]);
    ////DID REALLY DO ANYTHING?????????????????????????????????????????????????????????????????????????????????????????????????????
    bool inside_ignore_dist = (curr_distances_mm[i] <= IGNORE_DISTANCE_THRESHOLD_MM); 
    front_sensor_stuck_states[i] = (curr_distances_mm[i] != 0) && (within_stuck_dist || (within_tolerance && inside_ignore_dist) ); //
  }
  Serial.print(" stuck bools: " + strArray(front_sensor_stuck_states, NUM_F_U_SENSORS, false));

  //return isAllBool(sensor_stuck_states_array, true, NUM_F_U_SENSORS);
  return (numOccurances(front_sensor_stuck_states, true, NUM_F_U_SENSORS) >= (NUM_F_U_SENSORS-1)); // eg, at least (NUM_F_U_SENSORS-1) sensors have to be stuck
}


void determineDirection() {
  char max_dist_char_id;
  
  if (getMin(curr_distances_mm, NUM_F_U_SENSORS) == 0) { //the sensor which returns zero, actually has the largest distance, so grab that char id
    max_dist_char_id = F_ID_CHARS[minIndex(curr_distances_mm, NUM_F_U_SENSORS)]; 
    digitalWrite(ZERO_MEASUREMENT_LED_PIN, HIGH);
    Serial.print(" 0 return measurement ");

  } else {
    max_dist_char_id = F_ID_CHARS[maxIndex(curr_distances_mm, NUM_F_U_SENSORS)]; //find which sensor has the largest distance
    digitalWrite(ZERO_MEASUREMENT_LED_PIN, LOW);
  }

  
  bool is_left_right_in_tolerance = withinTolerance(curr_distances_mm[0], curr_distances_mm[2], LR_DIST_TOLERANCE_MM); 

  //Serial.print("is_left_right_in_tolerance: " + String(is_left_right_in_tolerance));
  //Serial.print(" maxChar: " + String(max_dist_char_id));

  if ((max_dist_char_id != 'F') && (!is_left_right_in_tolerance)) { //left/right has max distance... only change direction if there is significant difference between
    curr_turn_direction = max_dist_char_id;
  
  } else if (max_dist_char_id == 'F') { //front has maximum distance...
    curr_turn_direction = max_dist_char_id; 
  
  } else {
    //just keep going in same direction (which will be left/right)
  }
}


void loop() {
  U_current_time_ms = millis();

  if ((U_current_time_ms - U_previous_time_ms) >= TIME_BETWEEN_U_SENSORS_MS) {
    ////INPUTS
    //get distances
    getDistances();


    ////CALCULATIONS 
    ///speed control
    if (containsValueWithinRange(curr_distances_mm, 0, BRAKE_DISTANCE_THRESHOLD_MM, NUM_F_U_SENSORS)) { // make sure a zero measurement doesn't trigger it...
      /*
      if (!has_braked) { //this tries to prevent continual braking when not needed
        curr_drive_direction = 'B'; 
        has_braked = true;
        digitalWrite(VEHICLE_SLOW_SPEED_LED_PIN, HIGH);
        Serial.print(" BRAKING!!!");
      }*/
      
    } else if (containsValueWithinRange(curr_distances_mm, 0, SLOW_DOWN_DISTANCE_THRESHOLD_MM, NUM_F_U_SENSORS)) { // make sure a zero measurement doesn't trigger it...
      vehicle_speed = SLOW_SPEED;
      digitalWrite(VEHICLE_SLOW_SPEED_LED_PIN, LOW);
      Serial.print(" slow");
      
    } else {
      vehicle_speed = NORMAL_SPEED;
      digitalWrite(VEHICLE_SLOW_SPEED_LED_PIN, LOW);
      Serial.print(" normal");
    }

    ///stuck logic
    bool is_vehicle_currently_stuck  = isStuck();
    if (is_vehicle_currently_stuck) {
      //don't waste power on needlessly on motors
      curr_drive_direction = 'S'; 
      curr_turn_direction = 'C';
      digitalWrite(STUCK_LED_PIN, HIGH);

      Serial.print("...vehicle is stuck...");
      
    } else {
      curr_drive_direction = 'F';
      has_braked = false; 
      digitalWrite(VEHICLE_SLOW_SPEED_LED_PIN, LOW);
      determineDirection();
      digitalWrite(STUCK_LED_PIN, LOW);
    }

    //stuck_counter += (is_vehicle_currently_stuck) ? -1 : 1;
    if (is_vehicle_currently_stuck) {
      stuck_counter++;
    } else {
      stuck_counter--;
    }
    
    if (stuck_counter >= MAX_NUM_STUCK) {
      stuck_counter = 0;
      vehicle_is_definitely_stuck = true;
      
      curr_turn_direction = (rand()%2) ? 'L' : 'R';
      
    } else if (stuck_counter < 0 ) {
      stuck_counter = 0;
      //vehicle_is_definitely_stuck = false;
    }

    if (containsGreaterThanEqual(prev_distances_mm,REVERSE_DISTANCE_MM, NUM_F_U_SENSORS) 
        && containsGreaterThanEqual(curr_distances_mm,REVERSE_DISTANCE_MM, NUM_F_U_SENSORS)) {
      vehicle_is_definitely_stuck = false;
      Serial.println("Determined to be unstuck");
    }


    


    ////OUTPUTS
    //LED's
    if (!vehicle_is_definitely_stuck) { //if there is some ambiguity on definitely being stuck...
      if (is_vehicle_currently_stuck) {
        for (int i=0; i<NUM_F_U_SENSORS; i++) {
          digitalWrite(DIRECTION_LED_PINS[i], front_sensor_stuck_states[i]); //turn on the LEDs which correspond to the stuck ultrasonics
        }
      
      } else {
        int8_t pin_index = index(F_ID_CHARS, curr_turn_direction, NUM_F_U_SENSORS);
        for (int i=0; i<NUM_F_U_SENSORS; i++) {
          bool state = (i==pin_index);
          digitalWrite(DIRECTION_LED_PINS[i], state); //turn on the relevant direction LED, and off the others
        }
      }
    
    } else {
      Serial.println("Definitely stuck!");
      digitalWrite(STUCK_LED_PIN, stuck_flashing_state);
      digitalWrite(VEHICLE_SLOW_SPEED_LED_PIN, !stuck_flashing_state);
      curr_drive_direction = 'R';//overide
    }
    
 


    //make it go! (vroom vroom)    
    RC_Car.turn(curr_turn_direction, 255);
    RC_Car.drive(curr_drive_direction, vehicle_speed);
    
    //print results
    Serial.print(" | curr/prev distances: " + strArray(curr_distances_mm, NUM_F_U_SENSORS, false));
    Serial.print(", " + strArray(prev_distances_mm, NUM_F_U_SENSORS, false));
    Serial.print(" | turn dir: " + String(curr_turn_direction));
    Serial.print(" | drive dir: " + String(curr_drive_direction));
    Serial.print(" vehicle_speed: " + String(vehicle_speed));
    Serial.print("stuck_counter: " + String(stuck_counter));

    Serial.print("\n");

    U_previous_time_ms = U_current_time_ms; //boomark
    copyArray(curr_distances_mm, prev_distances_mm, NUM_F_U_SENSORS);
    stuck_flashing_state = !stuck_flashing_state; //flip
  }

}

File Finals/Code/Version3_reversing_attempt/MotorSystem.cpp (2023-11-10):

/*
 * 
 */


#include "MotorSystem.h"


MotorSystem::MotorSystem(bool print_results) {
  _PRINT_RESULTS = print_results;
  _PWM_SPEED_ENABLED = false; //default
}


void MotorSystem::attach(uint8_t steering_motor_a, uint8_t steering_motor_b, uint8_t driving_motor_a, uint8_t driving_motor_b) {
  _STEERING_MOTOR_A_PIN = steering_motor_a;
  _STEERING_MOTOR_B_PIN = steering_motor_b;
  _DRIVING_MOTOR_A_PIN = driving_motor_a;
  _DRIVING_MOTOR_B_PIN = driving_motor_b;

  pinMode(_STEERING_MOTOR_A_PIN, OUTPUT);
  pinMode(_STEERING_MOTOR_B_PIN, OUTPUT);
  pinMode(_DRIVING_MOTOR_A_PIN, OUTPUT);
  pinMode(_DRIVING_MOTOR_B_PIN, OUTPUT);
}


void MotorSystem::enablePWM(uint8_t steering_pwm_pin, uint8_t driving_pwm_pin) {
  _PWM_SPEED_ENABLED = true; 
  _STEERING_PWM_PIN = steering_pwm_pin;
  _DRIVING_PWM_PIN = driving_pwm_pin;

  pinMode(_STEERING_PWM_PIN, OUTPUT);
  pinMode(_DRIVING_PWM_PIN, OUTPUT);
}

void MotorSystem::_writeSpeed(uint8_t pwm_pin, uint8_t speed_val) {
  
  if (_PWM_SPEED_ENABLED) {
    if (_PRINT_RESULTS) Serial.print("analog writing!!!");
    analogWrite(pwm_pin, speed_val);
  } else {
    analogWrite(pwm_pin, 255); //default to HIGH
  }
}


//this method handles everything for driving
void MotorSystem::drive(char driving_direction_char, uint8_t speed_val) {
  _writeSpeed(_DRIVING_PWM_PIN, speed_val); 
  if (driving_direction_char == 'F') {
    if (_PRINT_RESULTS) Serial.print("...forward...");
    //forward
    digitalWrite(_DRIVING_MOTOR_A_PIN, HIGH);
    digitalWrite(_DRIVING_MOTOR_B_PIN, LOW);
    
  } else if (driving_direction_char == 'R') {
    if (_PRINT_RESULTS) Serial.print("...reverse..."); //was backward till brake was introduced
    //backward
    digitalWrite(_DRIVING_MOTOR_A_PIN, LOW);
    digitalWrite(_DRIVING_MOTOR_B_PIN, HIGH);
    
  } else if (driving_direction_char == 'B') {
    if (_PRINT_RESULTS) Serial.print("...BRAKE...");
    digitalWrite(_DRIVING_MOTOR_A_PIN, HIGH);
    digitalWrite(_DRIVING_MOTOR_B_PIN, HIGH);
    
  } else {
    if (_PRINT_RESULTS) Serial.print("...stop...");
    //stop - stop powering the drive motor
    digitalWrite(_DRIVING_MOTOR_A_PIN, LOW);
    digitalWrite(_DRIVING_MOTOR_B_PIN, LOW);
  }
  
  driving_direction = driving_direction_char; //update for future use
}

void MotorSystem::brake(uint8_t speed_val) {
  _writeSpeed(_DRIVING_PWM_PIN, speed_val); 
  digitalWrite(_DRIVING_MOTOR_A_PIN, HIGH);
  digitalWrite(_DRIVING_MOTOR_B_PIN, HIGH);
  driving_direction = 'B';
}


//this method handles everything for steering
void MotorSystem::turn(char turning_direction_char, uint8_t speed_val) {
  _writeSpeed(_STEERING_PWM_PIN, speed_val);
  if (turning_direction_char == 'L') {
    if (_PRINT_RESULTS) Serial.print("...left...");
    //forward
    digitalWrite(_STEERING_MOTOR_A_PIN, HIGH);
    digitalWrite(_STEERING_MOTOR_B_PIN, LOW);
    
  } else if (turning_direction_char == 'R') {
    if (_PRINT_RESULTS) Serial.print("...right...");
    //backward
    digitalWrite(_STEERING_MOTOR_A_PIN, LOW);
    digitalWrite(_STEERING_MOTOR_B_PIN, HIGH);
    
  } else { // 'C'
    if (_PRINT_RESULTS) Serial.print("...centre/stop...");
    //centre - spring system should centre the steering
    digitalWrite(_STEERING_MOTOR_A_PIN, LOW);
    digitalWrite(_STEERING_MOTOR_B_PIN, LOW);
  }
  
  turning_direction = turning_direction_char; //update for future use
}

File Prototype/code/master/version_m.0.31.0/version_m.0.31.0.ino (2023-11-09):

/*
 * Code modifications with ultrasonic, so that when distances 
 * are the same it probably means the vehicle is stuck.
 * 
 * Version m.0.31.0
 * 
 * Last updated 24 August 2023, Noah Lobbe
 */


#include "MotorSystem.h"
#include "biss0001_PIR.h"

////pin definitions

//motor driver
#define PWM_SPEED_ENABLED true 

#define EN_STEERING_SPEED_PIN 10
#define STEERING_MOTOR_A_PIN 4
#define STEERING_MOTOR_B_PIN 5

#define DRIVING_MOTOR_A_PIN 6
#define DRIVING_MOTOR_B_PIN 7
#define EN_DRIVING_SPEED_PIN 11

//PIR motion sensor
#define PIR_PIN 9
#define MOTION_LED_PIN 8 

//Ultrasonic sensor
#define ECHO_PIN 2
#define TRIGGER_PIN 3
#define STUCK_LED_PIN 12



////variables
#define PRINT_RESULTS true
#define GET_USER_INPUT false

//motor driver
bool determined_turn_direction = false; // so that the random direction doesn't keep changing for the same object
bool is_stuck = false;
#define STUCK_DISTANCE_MM 20
#define SPEED 200 //0-255 for motor PWM

//ultrasonic 
#define SPEED_OF_SOUND_MM_PER_S 340000
#define object_avoidance_distance_threshold_mm 1000 //these should probably be uppercase...
#define minimum_turning_distance_mm 900
#define STUCK_TOLERANCE 10//eg plus or minus 10 of current vs previous distances means the vehicle is probably stuck
uint16_t prev_distance_mm;


////objects
MotorSystem RC_Car(PRINT_RESULTS); //object to control the RC car motors
biss0001_PIR PIR_Sensor(PRINT_RESULTS); //pir motion sensor object


void setup() {
  ////setup pinModes and pin allocations
  
  //Motor driver stuff
  RC_Car.attach(STEERING_MOTOR_A_PIN, 
                STEERING_MOTOR_B_PIN, 
                DRIVING_MOTOR_A_PIN, 
                DRIVING_MOTOR_B_PIN);

  
  if (PWM_SPEED_ENABLED) {
    RC_Car.enablePWM(EN_STEERING_SPEED_PIN, EN_DRIVING_SPEED_PIN);
    
  } else {
    pinMode(EN_STEERING_SPEED_PIN, OUTPUT);
    pinMode(EN_DRIVING_SPEED_PIN, OUTPUT);
    digitalWrite(EN_STEERING_SPEED_PIN, HIGH); //default to max
    digitalWrite(EN_DRIVING_SPEED_PIN, HIGH); //default to max
  }

  //PIR motion sensor
  PIR_Sensor.attach(PIR_PIN);

  //Ultrasonc sensor
  pinMode(ECHO_PIN, INPUT);
  pinMode(TRIGGER_PIN, OUTPUT);
  digitalWrite(TRIGGER_PIN, LOW); //no accidental triggering
  pinMode(STUCK_LED_PIN, OUTPUT);

  
  ////Other stuff
  if (PRINT_RESULTS or GET_USER_INPUT) {       
    Serial.begin(9600);
    Serial.println("...Enter a two char command...");
    Serial.println("Drive motor \n\tMotor Select: 'D' \n\tcommands: F = forward, B = backward, S = stop"
                   "\nSteering motor \n\tMotor Select: 'S' \n\tcommands: L = left, R = right, C = centre");
  }

  randomSeed(analogRead(0));//make sure A0 doesn't have anything on it!!!
}


void userMotorControl() {
  ////Function to handle the user controling the motor system
  if (Serial.available() > 0) {
    String input = Serial.readString();
    char motor_select = input[0];
    char command = input[1];
    int speed_value = (input.substring(2).toInt()); //converting
    String text = "\nYou inputted..."
                  "\n\tmotor select: " + String(motor_select) +
                  "\n\tcommand: " + String(command) +
                  "\n\tspeed value: " + String(speed_value);
    Serial.println(text);

    if (motor_select == 'D') {
      Serial.println("Command given to drive motor...");
      RC_Car.drive(command, speed_value);
      
    } else if (motor_select == 'S') {
      Serial.println("Command given to steering motor...");
      RC_Car.turn(command, speed_value);
      
    } else {
      Serial.println("...unrecognized motor_select...");
    }
  }
}

bool withinTolerance(uint16_t value, uint16_t previous_value, uint16_t tolerance) {
  if (abs(value - previous_value) <= tolerance) { //https://www.mathsisfun.com/numbers/absolute-value.html
    return true;
  } else {
    return false;
  }
  
}


void loop() {
  ////inputs
  if (GET_USER_INPUT) {
    userMotorControl();
  }

  //PIR motion sensor
  PIR_Sensor.checkSensor(); 

  //Utlrasonic sensor
  digitalWrite(TRIGGER_PIN, HIGH);
  delayMicroseconds(10); //send the trigger pulse
  digitalWrite(TRIGGER_PIN, LOW);


  ////Calculations
  
  //Ultrasonic sensor
  uint16_t duration_uS = pulseIn(ECHO_PIN, HIGH, 0); //Time (in microseconds, uS) how long the ECHO pin pulse is HIGH
  uint16_t distance_mm = 0.5 * SPEED_OF_SOUND_MM_PER_S * duration_uS * 1e-6; //conversions done inline to prevent inaccuracies through rounding


  ////outputs
  if (PRINT_RESULTS) {
    Serial.print("\nuS: " + String(duration_uS) + " | distance (mm): " + String(distance_mm) + " | prev_distance: " + String(prev_distance_mm));
  }

  /*
  if (PIR_Sensor.pir_state) {
    time_to_escape = true;
    digitalWrite(MOTION_LED_PIN, HIGH);
    
  } else {
    time_to_escape = false;
    digitalWrite(MOTION_LED_PIN, LOW);
  }
  */

  ////Control algorithm

  //check if stuck first
  if (withinTolerance(distance_mm, prev_distance_mm, STUCK_TOLERANCE) && (distance_mm <= STUCK_DISTANCE_MM)) {
    if (PRINT_RESULTS) Serial.print("...STUCK...");
    is_stuck = true;
    digitalWrite(STUCK_LED_PIN, HIGH);
    RC_Car.drive('S', SPEED);
    
  } else {
    is_stuck = false;
    digitalWrite(STUCK_LED_PIN, LOW);
  }

  //when not stuck and motion has been detect then it is time to escape!
  if (!is_stuck) { //&& time_to_escape
    //obstacle avoidance algorithm
    
    if (distance_mm <= object_avoidance_distance_threshold_mm) { //avoid object
      char direction_char;
      if (!determined_turn_direction) { 
        if (random(0,100) >= 50) { // currently has no method of determine whether left/right is better, so random!
          direction_char = 'R';
        } else {
          direction_char = 'L';
        }
        determined_turn_direction = true;
      }
      RC_Car.turn(direction_char, 255);

      
    } else if (distance_mm <= minimum_turning_distance_mm) { //not enough space to avoid object, so halt
      RC_Car.drive('S', SPEED); 
      RC_Car.turn('C', 255);
      
       
    } else { //just drive forward, thats the best way to escape when there are no obstacles :D
      determined_turn_direction = false; //reset because
      
      if (RC_Car.turning_direction != 'C') { //don't need to turn anymore
        RC_Car.turn('C', 255); 
      }
    
      if (RC_Car.driving_direction != 'F') { //drive forward because there is nothing in the way
        RC_Car.drive('F', SPEED); 
      }
    }
    
  } else { //what to do if stuck...
    //something!
  }



  prev_distance_mm = distance_mm; //update for next loop iteration
  delay(60); //to prevent sensor's sound waves from interfering with itself. Could probably implement a timer instead
}
